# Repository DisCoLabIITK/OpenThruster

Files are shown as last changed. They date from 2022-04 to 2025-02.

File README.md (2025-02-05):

# OpenThruster
Open source 3D printed thruster for AUVs and ASVs.
---------------------------------------------------------------------------------------------------
3D Render:

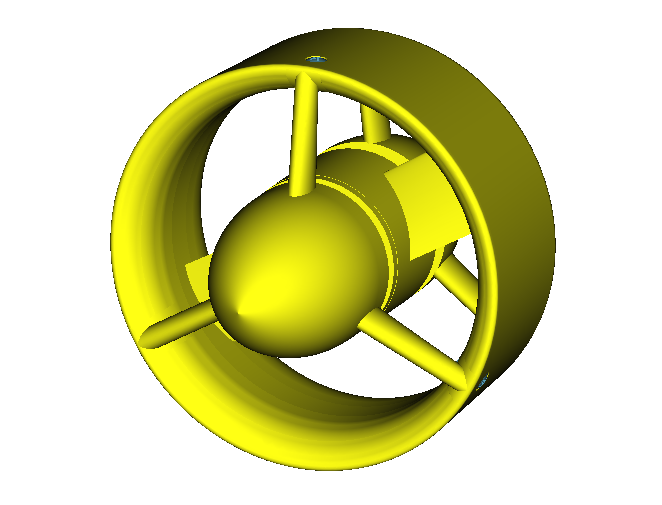
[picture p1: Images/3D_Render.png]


Exploded View:

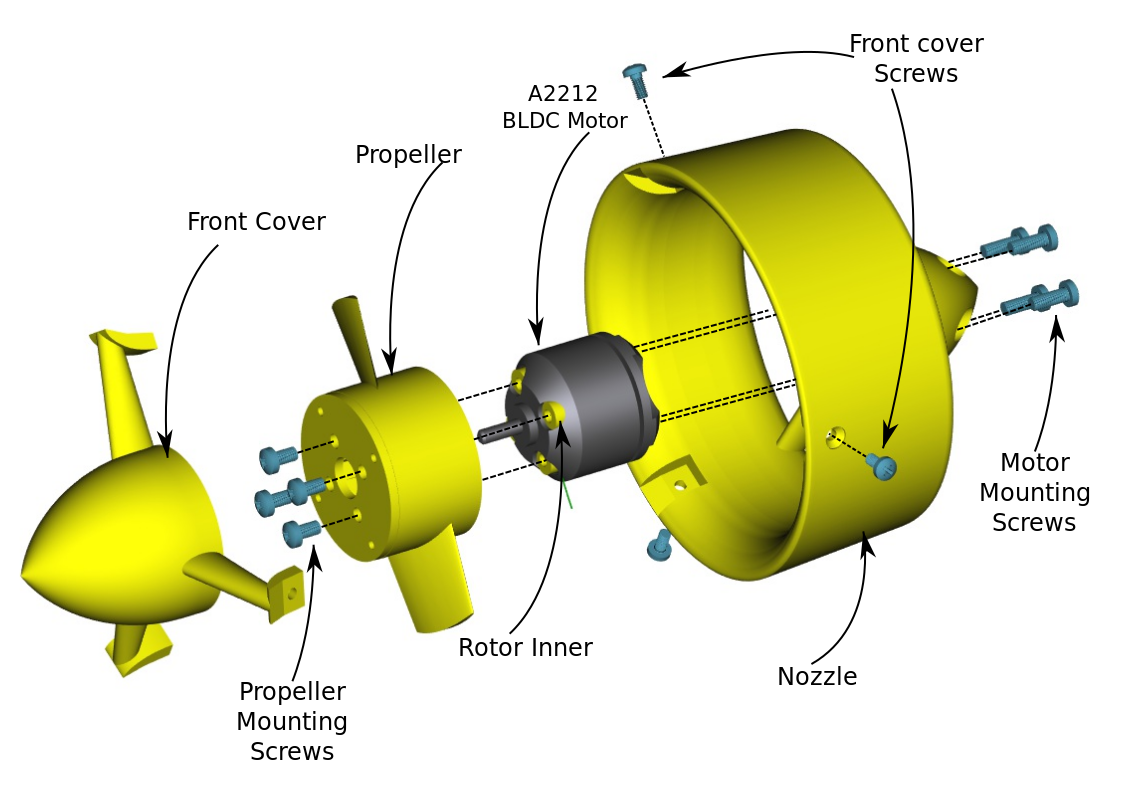
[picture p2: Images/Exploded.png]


Final Assembled:



Assembly
--------------------------------------------------------------------------------------------------
Assembly details on the Wiki page: [https://github.com/DisCoLabIITK/OpenThruster/wiki](https://github.com/DisCoLabIITK/OpenThruster/wiki/Assembly-Instructions)

The 3D printable STL files are in the STL folder.
--------------------------------------------------------------------------------------------------
Print settings for Nozzle:
* 0.4mm Extruder nozzle
* 0.2mm layer height
* 30% Infill (Gyroid)
* 4 Perimeters
* 6mm Brim.

Print settings for Propeller: 
* 0.1mm layer height
* 0.2-0.4mm Extruder nozzle
* Supports enabled
* 4 Perimeters
* Solid infill.

FreeCAD source files in FreeCAD source files folder. FreeCAD v0.19 was used for old design. New design files for FreeCad v1.0 are added in separate folder.

OpenProp source files downloaded from : https://openprop.engineering.dartmouth.edu/. The folder uploaded here has the modified option of NACA001612 and 001615 profiles.

Bill of Materials
--------------------------------------------------------------------------------------------------
1. PLA / ABS Filament for printing the propeller, nozzle, top cover and motor inner.
2. 3x M2.5 5mm Screws - Front Cover Screws
3. 4x M3 8mm Screws - Motor Mounting Screws
4. 1x A2212 1000KV BLDC Motor and the 4 screws (Propeller mounting screws in figure above) that come with it.
5. 1x 30A ESC with reversing capability

Testing Video: 
--------------------------------------------------------------------------------------------------
https://drive.google.com/file/d/1CwWSbAQDMGnaGXgHJ6uAxaj82aNr3GoJ/view?usp=sharing

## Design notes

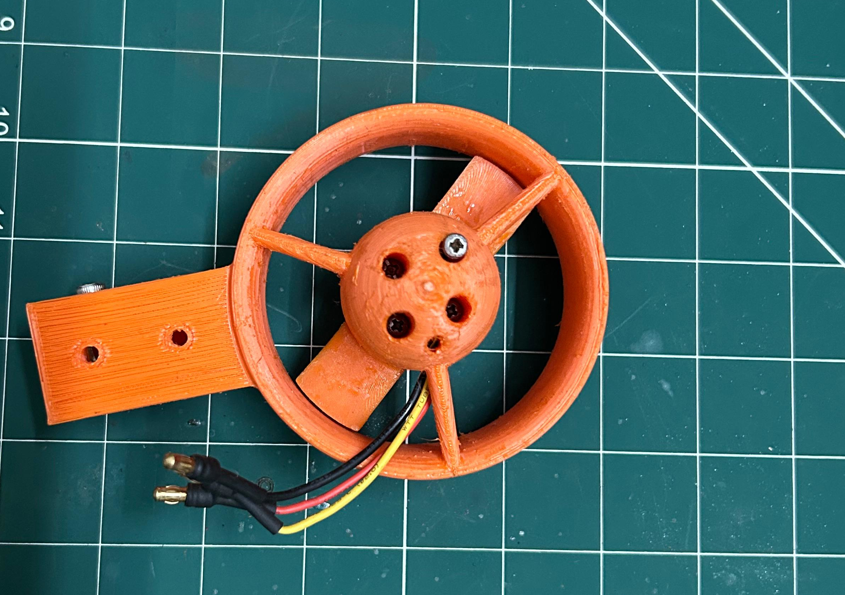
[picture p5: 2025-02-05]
Images/Motor_Nozzle_Screw.jpeg

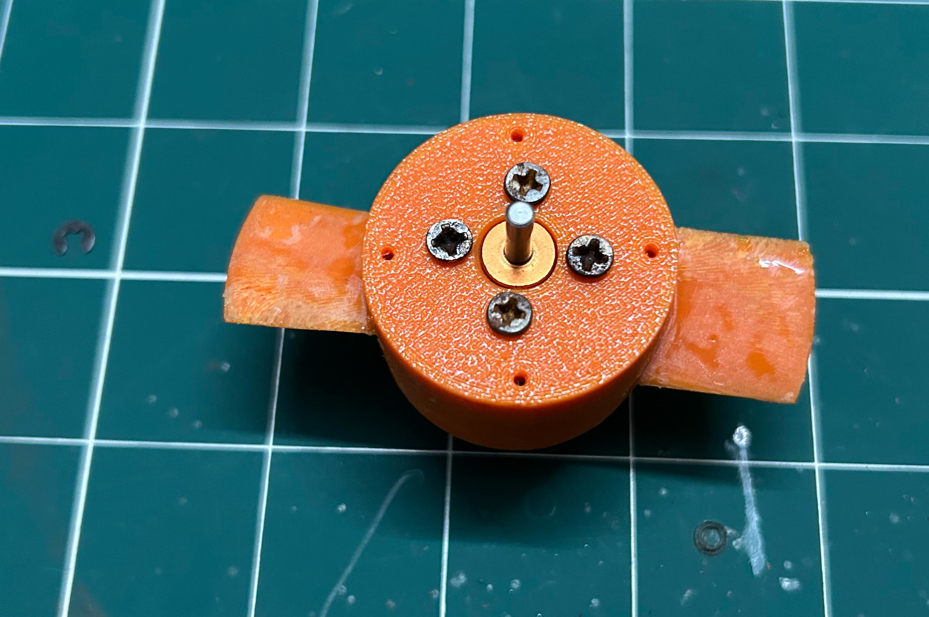
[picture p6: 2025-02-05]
Images/Propeller_Screw.jpeg

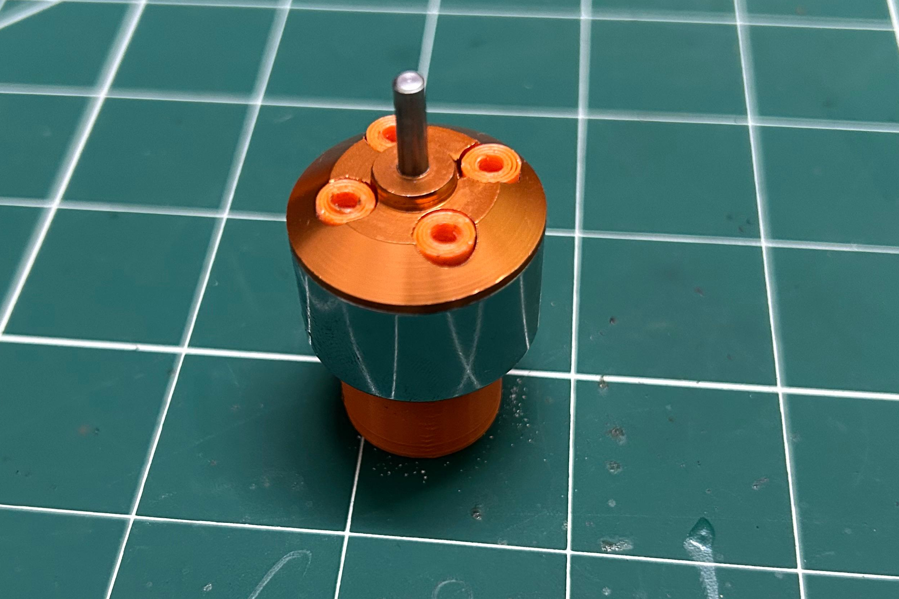
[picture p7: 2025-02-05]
Images/Use_Helper.jpeg

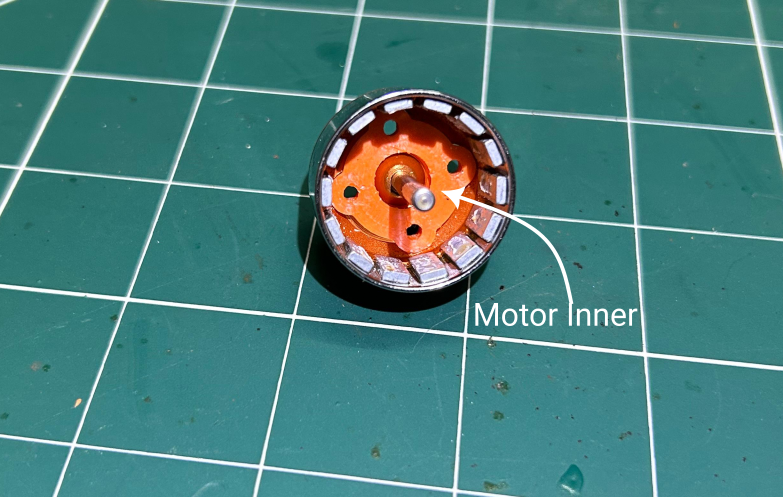
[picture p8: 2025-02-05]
Images/Insert_Inner.png

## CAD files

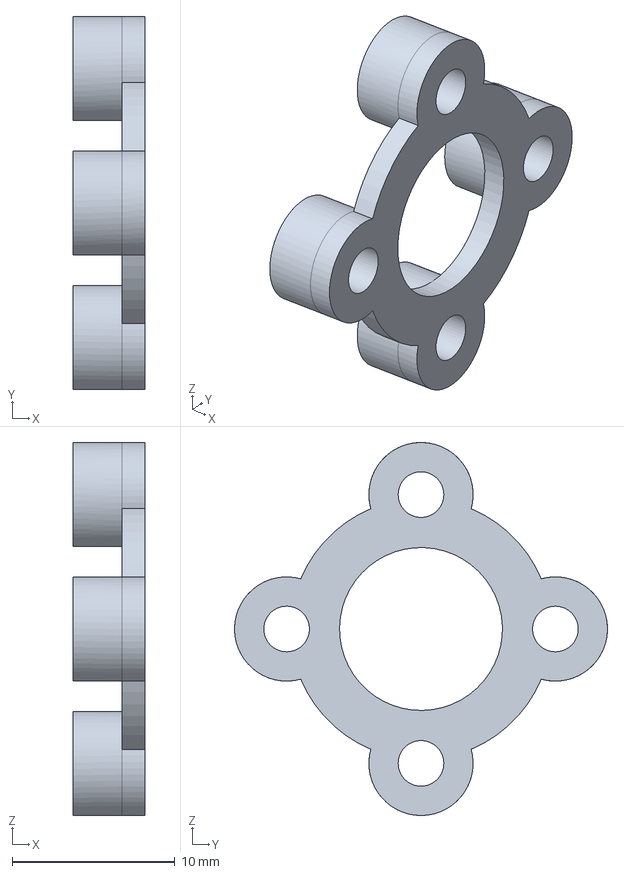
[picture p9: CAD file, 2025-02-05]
FreeCad_v_1.0_Source_Files/Motor_Inner_v2.FCStd
4.40 x 22.9 x 22.9 mm

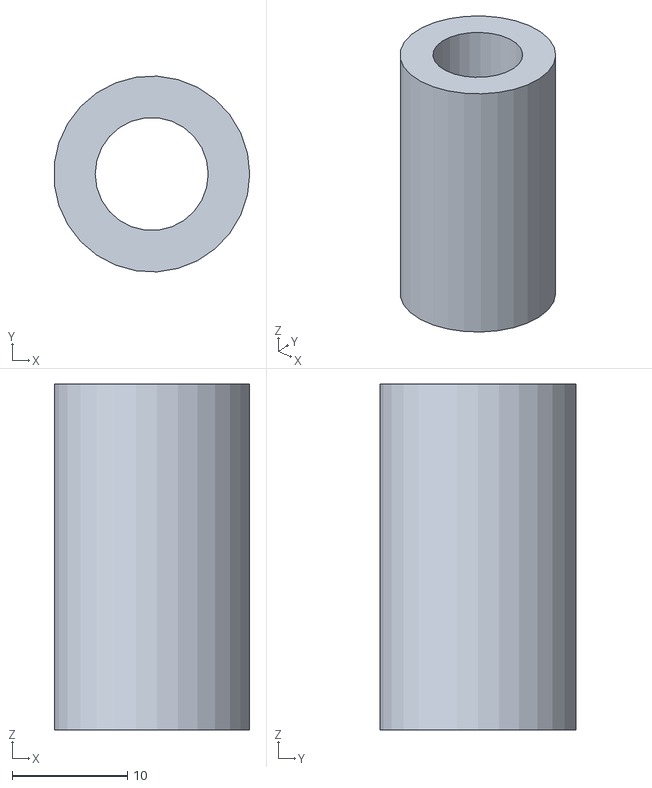
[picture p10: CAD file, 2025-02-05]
STL/Motor_Inner_Install_Helper.stl
17.0 x 17.0 x 30.0

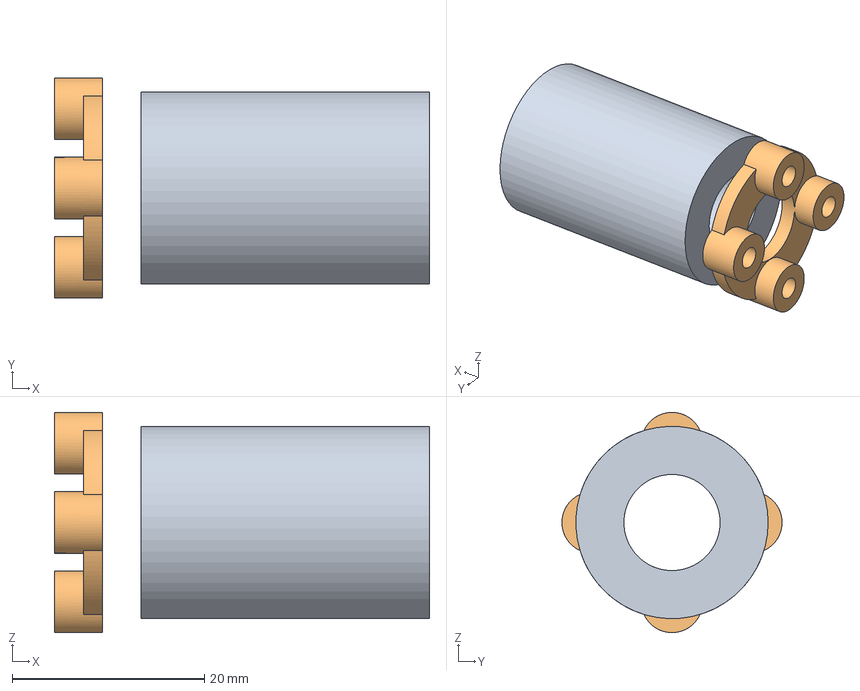
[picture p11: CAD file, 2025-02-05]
FreeCad_v_1.0_Source_Files/Motor_inner_Helper.FCStd
39.0 x 22.9 x 22.9 mm
Motor_Inner

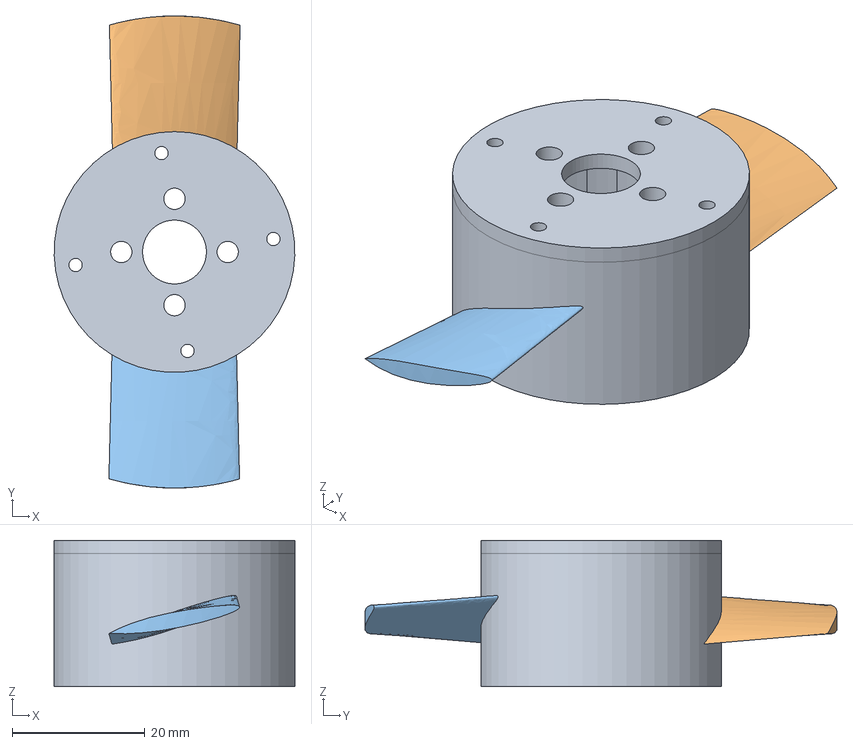
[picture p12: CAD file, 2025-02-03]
FreeCad_v_1.0_Source_Files/Prop-CCW.FCStd
36.2 x 71.0 x 22.0 mm
Hub
Blade1
Blade2

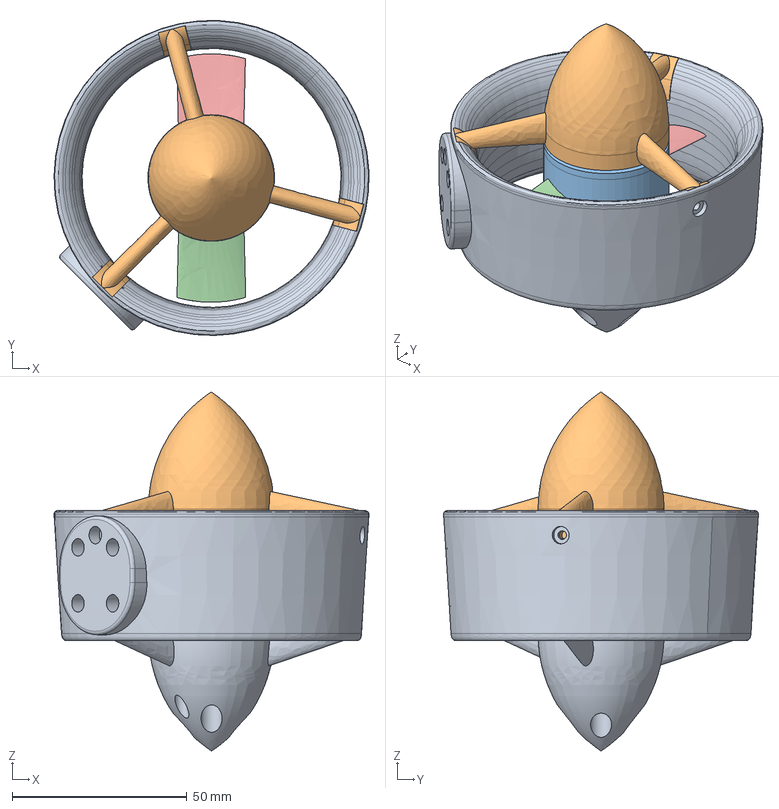
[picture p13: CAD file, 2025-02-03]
FreeCad_v_1.0_Source_Files/Thruster_ROV.FCStd
90.0 x 90.0 x 102.6 mm
Thruster_Nozzle001
Front_Cover
Hub
Blade2 (Mirror #1)
Blade1 (Mirror #2)

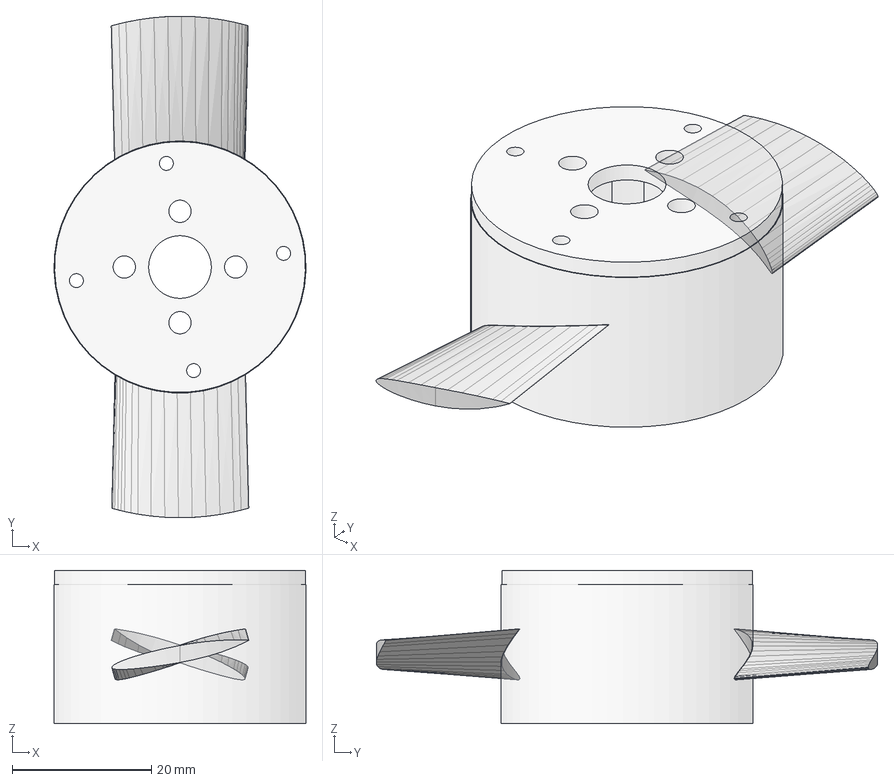
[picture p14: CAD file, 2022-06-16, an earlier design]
FreeCad_v_0.19_Source_Files/C4-28-5000-Thick-NonOpt-CW.FCStd
36.2 x 72.0 x 22.0 mm
NACA16-12
NACA16-013

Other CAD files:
STL/Motor_Inner.stl
STL/Prop-CW.stl
STL/Prop-CCW.stl
FreeCad_v_1.0_Source_Files/Prop-CW.FCStd
FreeCad_v_0.19_Source_Files/C4-28-5000-Thick-NonOpt-CCW.FCStd

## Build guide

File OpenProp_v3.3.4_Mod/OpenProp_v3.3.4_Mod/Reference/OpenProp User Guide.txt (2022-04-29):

OpenProp User Guide
10/21/2013

Prof. Brenden Epps,     Thayer School of Engineering at Dartmouth College
Prof. Richard Kimball,  Maine Maritime Academy

------------------------------------------------------------------------------------------------
Setup:

1. Download OpenProp_v3.3.3.zip from the OpenProp website: http://engineering.dartmouth.edu/openprop .  

2. Move the zip file to any convenient parent directory:
 	(e.g. <parent> == /Users/bepps/Documents/) 

3. Unzip OpenProp_v3.3.3.zip.  The "OpenProp" folder should now appear in the "parent" directory: 
	(e.g. <OpenProp> == /Users/bepps/Documents/OpenProp_v3.3.3/)

------------------------------------------------------------------------------------------------
Running OpenProp at the command line:

1. OpenProp can be run at the Matlab command line using various function calls.  The usage 
   is illustrated in the examples folders:

	./Examples/Ex*

2.  Use the templates in the Example folders to get started on your design.  The basic commands
    are as follows:
	>> Run_input_script, 			       (creates pt data structure and pt.input)
	>> pt.design   = EppsOptimizer(pt.input);
	>> pt.states   = Analyze(pt,[0:0.1:10]);
	>> pt.geometry = Geometry(pt);

3. Users are encouraged to create a new folder for each propeller/turbine design they create.  

------------------------------------------------------------------------------------------------
Running OpenProp using the graphical user interface (GUI):

1. OpenProp can also be run using the graphical user interface (GUI).

2. In Matlab, change the working directory to the "OpenProp" folder. 

3. At the command line, type:
	 >> openprop

	This loads the Single Design GUI.  

4. To perform a single propeller/turbine design, input the desired inputs to the GUI, and 
   press the "Run OpenProp" button.

   To perform a parametric design study, choose "Parametric Study" from the pull-down menu in
   the top left corner of the GUI.

------------------------------------------------------------------------------------------------
GUI file structure and data input/output:

1. In OpenProp, all propeller/turbine data is saved in a data structure called "pt".  

2. Upon execution of a "Single Design" or "Parametric Study", OpenProp will look for the
   directory <OpenProp>/filename/ and will create that directory if it does not exist:
  	(e.g. /Users/bepps/Documents/OpenProp_v3.3.2/DefaultPropeller)

   The pt data structure is always saved in <OpenProp>/filename/filename.mat .

   NOTE: When running a "Single Design", the following data structures are overwritten:
		pt.filename
		pt.date
		pt.input
		pt.design
		pt.geometry
		pt.states
	When running a "Parametric Study", the following data structures are overwritten:
		pt.name
		pt.date
		pt.parinput
		pt.paroutput

	In order to avoid overwriting previous designs, change the "filename".

3. In the "Single Design" and "Parametric Study" modes, the GUI values can be saved by 
   pressing the "Save" button.  This creates the following files:

	<OpenProp>/filename/filename_GUIsd.mat   -- "Single Design"    GUI values
	<OpenProp>/filename/filename_GUIps.mat   -- "Parametric Study" GUI values

   Similarly, prior GUI values can be loaded using the "Load" button and then choosing the
   appropriate GUI mat file. 

   NOTE: These files are automatically created/overwritten at runtime (i.e. when the 
         "Run OpenProp" button is pressed).

4. After running OpenProp, the "pt" data structure can be loaded into the Matlab workspace by:
    	>> change the working directory to <OpenProp>/filename
	>> load filename.mat

------------------------------------------------------------------------------------------------
Command line data input/output:

1. In OpenProp, all propeller/turbine data is saved in a data structure called "pt". 
   When running at the command line, the user may choose to use shorthand for the 
   "input", "design", "geometry", and "states" data structures, as follows:
	pt = 
		pt.filename
		pt.date
		pt.i
		pt.d
		pt.g
		pt.s

	For an example of this notation, see ExP02_Propeller_Parametric_Study.

2. The default inputs are listed in OpenProp_default_inputs.m, and the default input data 
   structure is as follows.  Here, "999" indicates that a value must be specified by the user.
   The user can create in input data structure that contains some or all of the other optional
   inputs.  See EppsOptimizer.m, Analyze.m, Geometry.m, and AnalyzeGeometry.m to understand the usage of these inputs.

	-----------------------------------
	input =
                part1: '------ Performance inputs ------'
                    L: 999  (only used in turbine   case)	% tip speed ratio     (for propeller, L  = pi/Js)
                   Js: 999  (only used in propeller case)	% advance coefficient (for turbine,   Js = pi/L )
                   CT: 999  (only used in propeller case)	% desired total thrust coefficient (propeller plus duct)         (user may specify 'KT' or dimensional 'THRUST' instead)
                   CQ: 999  (only used in propeller case)	% desired total torque coefficient (optional, in lieu of 'CT')   (user may specify 'KQ' or dimensional 'TORQUE' instead)
								% Note: The    user must specify one of {'CT', 'KT', or 'THRUST'} to minimize torque for prescribed thrust,
								%       or the user must specify one of {'CQ', 'KQ', or 'TORQUE'} to maximize thrust for prescribed  torque. 
								% Note: For turbine case, 'CT' and 'CQ' are unnecessary and are ignored
                part2: '------ Geometry inputs ------'
                    Z: 999 					% number of blades
             Meanline: 'NACA a=0.8 (modified)'			% meanline  form  (may be given as cell array of same length as XR)
            Thickness: 'NACA 65A010'				% thickness form  (may be given as cell array of same length as XR)
                part3: '------ Blade/Inflow inputs ------'
                   XR: [1x10 double]				% radial ordinate / R 
                 XCoD: [1x10 double]				% chord / D 			at XR
                Xt0oD: [1x10 double]				% thickness / D			at XR
                t0oc0: 0.1   * [1 1 1 1 1 1 1 1 1 1]		% thickness / chord		at XR (optional, in lieu of Xt0oD) 
                  XCD: 0.008 * [1 1 1 1 1 1 1 1 1 1]		% section drag coefficient	at XR
                  XVA: [1 1 1 1 1 1 1 1 1 1]			% axial inflow velocity / Vs	at XR
                  XVT: [0 0 0 0 0 0 0 0 0 0]			% swirl inflow velocity / Vs	at XR
                 dXVA: [0 0 0 0 0 0 0 0 0 0]			% variation in axial inflow velocity / Vs at XR (for cavitation analysis)
               XCLmax: [1x10 double]				% max lift coefficient	at XR       (for chord optimization)
                   ri: [1x10 double]				% [m] radial ordinate in dimensional units!         (optional)
                  VAI: [1 1 1 1 1 1 1 1 1 1]			% axial inflow velocity / Vs              at ri (optional, in lieu of  'XVA')
                  VTI: [0 0 0 0 0 0 0 0 0 0]			% swirl inflow velocity / Vs              at ri (optional, in lieu of  'XVT')
                 dVAI: [0 0 0 0 0 0 0 0 0 0]			% variation in axial inflow velocity / Vs at ri (optional, in lieu of 'dXVA')
                part4: '------ Computational inputs ------'
       Propeller_flag: 999					% 0 == turbine, 1 == propeller
         Viscous_flag: 999					% 0 == viscous forces off (CD = 0), 1 == viscous forces on
             Hub_flag: 0					% 0 == no hub, 1 == hub
            Duct_flag: 0					% 0 == no duct, 1 == duct
           Chord_flag: 0					% 0 == do not optimize chord lengths, 1 == optimize chord
            Plot_flag: 0					% 0 == do not display plots, 1 == display plots
            Wake_flag: 0					% 0 == Horseshoe(...,Wrench(...)) analytic formulae, 1 == Wake_Horseshoe(...) numerical model
 EppsOptimizer02_flag: 1   (only used in propeller case)	% Propeller optimization method (choose one only): LL-Linear
 EppsOptimizer23_flag: 0   (only used in propeller case)	% Propeller optimization method (choose one only): LL-Newton (standard    hub drag model)
 EppsOptimizer53_flag: 0   (only used in propeller case)	% Propeller optimization method (choose one only): LL-Newton (variational hub drag model)
      Make2Dplot_flag: 1					% 1 == make 2D geometry plot
      Make3Dplot_flag: 1					% 1 == make 3D geometry plot 
      Make_Rhino_flag: 0					% 1 == make Rhino file
      Make_SWrks_flag: 0					% 1 == make SolidWorks file
    QuarterChord_flag: 0					% 0 == lifting line at mid-chord, 1 == lifting line at mid-chord (for geometry only)
            LSGeoCorr: 'none'					% propeller Lifting Surface Geometry Corrections		
          ChordMethod: 'CLmax'					% Method of chord optimization {'CLmax', 'ConeyPLL', 'FAST2011dCTP', 'FAST2011dVAC'}
		  EAR: 0 					% Expanded Area Ratio specification (for chord optimization), ignored if EAR = 0
                   Mp: 20					% number of panels radially
                   Np: 20					% number of panels chordwise
                 ITER: 50					% number of iterations in solvers 
                  HUF: 0					% hub unloading factor
                  TUF: 0					% tip unloading factor
                  Rhv: 0.5					% hub vortex radius / hub radius
           ALPHAstall: 8*pi/180					% [rad] stall angle of attack
                part5: '------ Dimensional inputs (SI units) ------'
                   Vs: 1					% [m/s] free-stream speed
                    R: 1					% [m]	rotor radius (may give     diameter D    instead)
                 Rhub: 0.2000					% [m]   hub radius   (may give hub diameter Dhub instead)
                   Dm: 2					% [m]   model diameter 
                  rho: 1000					% [kg/m^3] fluid density
                    H: 3.0480					% [m]   shaft centerline depth (for cavitation analysis)
                    g: 9.8100					% [m/s^2] gravitational constant (for cavitation analysis)
                 Patm: 101325					% [Pa]  atmospheric pressure (for cavitation analysis)
                   Pv: 2500					% [Pa]  vapor pressure (for cavitation analysis)
                part6: '------ Duct inputs ------'
             Rduct_oR: 1					% duct radius  			 (user may specify dimensional 'Rduct' instead)
             Cduct_oR: 1					% duct chord length		 (user may specify dimensional 'Cduct' instead)
             Xduct_oR: 0					% duct axial position downstream (user may specify dimensional 'Xduct' instead)
                  CDd: 0.008					% duct drag coefficient
                  TAU: 1      (only used in propeller case)	% thrust ratio == propeller thrust / total thrust 
	          CTD: 0      (only used in turbine   case)     % desired duct thrust coefficient for turbine case (user may specify 'KTD' or dimensional 'THRUSTduct' instead)

	-----------------------------------
	design = 

        part1: '------ Section properties, size (1,Mp) ------'
           RC: [1x20 double] 					% radial coordinate of control points / R
           DR: [1x20 double] 					% delta(RV)
            G: [1x20 double] 					% circulation / (2*pi*R*Vs)
          VAC: [1x20 double] 					%      axial free-stream speed / Vs
          VTC: [1x20 double]					% tangential free-stream speed / Vs
       UASTAR: [1x20 double] 					%      axial inducted velocity / Vs
       UTSTAR: [1x20 double] 					% tangential inducted velocity / Vs
        VSTAR: [1x20 double] 					% total inflow speed / Vs
        TANBC: [1x20 double] 					% tangent of free-stream  inflow angle, Beta
       TANBIC: [1x20 double] 					% tangent of wake-aligned inflow angle, BetaI
           CL: [1x20 double] 					% section lift coefficient
           CD: [1x20 double] 					% section drag coefficient
          CoD: [1x20 double] 					% chord / diameter
         t0oc: [1x20 double] 					% thickness / chord
         t0oD: [1x20 double] 					% thickness / diameter
        part2: '------ Other properties  ------'
    converged: 1		 				% 1 == solver converged, 0 == solver did not converge
    iteration: 7	 					% iteration number at conclusion of solver
           RV: [1x21 double] 					% radial coordinate of vortex lattice points / R
      Rhub_oR: 0.2000 						% Rhub / R
          EAR: 0.6058 						% expanded area ratio
           LM: -0.3950 						% Lagrange multiplier
         VMIV: 1.0000 						% volumetric mean inflow velocity / Vs
         VMWV: 1.1825 						% volumetric mean wake   velocity / Vs
       SIGMAs: 257.4518 					% cavitation number
        part3: '------ Performance metrics ------'
            L: 3.7714 						% tip speed ratio
           Js: 0.8330 						% advance coefficient
           KT: 0.1500 						% thrust  coefficient
           KQ: 0.0283 						% torque  coefficient
           CT: 0.5505 						% thrust  coefficient
           CQ: 0.2076 						% torque  coefficient
           CP: 0.7831 						% power   coefficient
          CTH: -0.0077 						% hub thrust coefficient
         EFFY: 0.7030 						% efficiency
       ADEFFY: 0.8908 						% actuator disk efficiency
           QF: 0.7892 						% quality factor (EFFY/ADEFFY)

	-----------------------------------
 	states = 

        part1: '------ Off-design states ------'
            L: [18x1 double]					% tip speed ratio
           Js: [18x1 double]					% advance coefficient
           RC: [1x20 double]					% radial coordinate of control points / R
          CoD: [1x20 double]					% section chord length / rotor diameter
            G: [18x20 double]
       UASTAR: [18x20 double]					% ALL OTHERS SAME AS "design"
       UTSTAR: [18x20 double]
        VSTAR: [18x20 double]
        TANBC: [18x20 double]
       TANBIC: [18x20 double]
        ALPHA: [18x20 double] 					% net angle of attack
           CL: [18x20 double]
           CD: [18x20 double]
        part2: '------ Numerical metrics ------'
    converged: [18x1 double]
    iteration: [18x1 double]
        part3: '------ Performance metrics ------'
           KT: [18x1 double]
           KQ: [18x1 double]
           CT: [18x1 double]
           CQ: [18x1 double]
           CP: [18x1 double]
         EFFY: [18x1 double]
         VMWV: [18x1 double]

	-----------------------------------
	ginput =
                part1: '------ Design piont inputs ------'
                    L: 999  (only used in turbine   case)	% design point tip speed ratio     (for propeller, L  = pi/Js)
                   Js: 999  (only used in propeller case)	% design point advance coefficient (for turbine,   Js = pi/L )
								% Note: If the design point is unknown, use Js = pitch/diameter at blade tip

                part2: '------ Rotor geometry inputs ------'
                    Z: 999 					% number of blades
              Rhub_oR: 999   % the user must specify one of the following: {Rhub_oR or (Rhub and R) or (Dhub and D) or Dhub_oD}

                part3: '------ Blade/Inflow inputs ------'

Note: The blade geometry table must be given either versus raw radii 'XR' or control point radii 'RC'
                   XR  		RC				% radial ordinate / R   
           (computed)    	RV               		% vortex point radii / R
           (computed)    	DR               		% vortex panel width / R
                 XCoD  		CoD				% chord / D 			
  (XPoD or XTHETArad) 		(PoD or THETArad)		% pitch/diameter or pitch angle [rad]
                  XVA   	VAC				% axial inflow velocity / Vs
                  XVT  	 	VTC				% swirl inflow velocity / Vs                
                   Mp						% number of panels radially (default Mp = 20)
           
Note: IF CLCD_flag == 0, then the Meanline and Thickness distributions must be given to determine the lift and drag characteristics
                  XCD   	CD				% section drag coefficient	at XR
                f0oc0   	f0oc    			% section camber / chord at XR
      (Xt0oD or t0oc0)		t0oc				% thickness / D  or  thickness / chord  at XR 
            dCLdALPHA		dCLdALPHA  			% lift curve slope [default: dCLdALPHA = 2*pi/(1 + 2/PAR) ], where PAR = propeller aspect ratio (computed)
 
      For both the XR or RC data tables, the user must also provide either:
 
            {'f0octilde','CLItilde', and 'alphaItilde'} 	% {ideal camber, ideal lift coefficient, and ideal angle of attack} versus XR or RC
      or    {'Meanline' and 'Thickness'}			% meanline and thickness forms, which may be given as cell array of same length as XR or RC

      ELSE  CLCD_flag == 1, then the lift and drag coefficients must be given, tabulated versus radius and angle of attack:     
                            Note: angle of attack is measured relative to blade pitch angle THETArad, such that ALPHA == 0 when the inflow angle BetaIC equals THETArad   
         	      RELMdata      				% M == number of RELM  radii            (typically RELM == XR, but RELM can by any radii)        
        	     ALPHAdata  				% N == number of ALPHA angles of attack 
           		CLdata  				% CL(RELM,ALPHA) data matrix, size[M,N]
          		CDdata  				% CD(RELM,ALPHA) data matrix, size[M,N]      
      ENDIF

                part4: '------ Computational inputs ------'
       Propeller_flag: 999					% 0 == turbine, 1 == propeller
         Viscous_flag: 999					% 0 == viscous forces off (CD = 0), 1 == viscous forces on
             Hub_flag: 0					% 0 == no hub, 1 == hub
            Duct_flag: 0					% 0 == no duct, 1 == duct
            Plot_flag: 0					% 0 == do not display plots, 1 == display plots
            Wake_flag: 0					% 0 == Horseshoe(...,Wrench(...)) analytic formulae, 1 == Wake_Horseshoe(...) numerical model
            CLCD_flag: 0                                        % 0 == use CLCD_vs_ALPHA.m , 1 == use CL and CD data given in ginput
            LSGeoCorr: 'Morgan1968'  (propeller default)	% propeller Lifting Surface Geometry Corrections {'none', 'Morgan1968', 'EckhardtMorgan1955', 'vanManen1958'}		
            LSGeoCorr: 'none'        (turbine   default)	% propeller Lifting Surface Geometry Corrections - not recommended with turbines	
                 ITER: 50					% number of iterations in solvers 
                  Rhv: 0.5					% hub vortex radius / hub radius
           ALPHAstall: 8*pi/180					% [rad] stall angle of attack

------------------------------------------------------------------------------------------------	
Tips and tricks:

1. To save keystrokes, unpack the pt data structure.  For example, to plot the design
   circulation distribution:
   
	>> d = pt.design;
	>> figure,
	>> plot(d.RC,d.G)

    Or to plot a turbine performance curve:

	>> s = pt.states;
	>> figure,
	>> plot(s.L,-s.CP)

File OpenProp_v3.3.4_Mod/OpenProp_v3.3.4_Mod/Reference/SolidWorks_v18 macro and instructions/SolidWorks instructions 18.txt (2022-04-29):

SolidWorks instructions:
Created: Rob Damus,     9/24/2009
 Edited: Brenden Epps, 10/ 6/2009 

Follow these steps to create a solid propeller blade in SolidWorks:

___ Create your hub ----

1. Draw the hub in SolidWorks, and save it in a SolidWorks part document file

2. Copy your hub file and rename it something like hub_with_blades.swp

3. Open hub_with_blades.swp

4. Run the following steps to add the key blade to the hub:

--- Create the key blade ----

1. Export filename_SolidWorks.txt from the OpenProp Geometry function.
	-- Make sure that the trailing edge point (2Np-1) is the same as point (1), so all blade sections are closed contours.

2. Run the OpenProp SolidWorks macro:
	-- (In SolidWorks)  Tools > Macro > Edit
	-- Open SolidWorks_macro_v18.swp
	-- Press the play button
	-- This should result in a sketch of blade sections and guide curves over surface points.

3. Create Surface Loft of the SectionCurve1...SectionCurve21
	-- Select all 21 SectionCurves in the Feature Manager
	-- Insert > Surface > Loft  (orange loft button)
 	-- Select GuideCurves 1-6.  GuideCurve 7 is an artifact of Solidworks_macro_v14 and should be ignored in macro v18.
	-- Check "Merge tangent faces"
	-- Uncheck "Close loft"

3. Create Surface-Fill at tip
	-- Insert > Surface > Fill
	-- For Patch Boundary: select TipSectionCurve21
	-- For Constraint Curves: select all TipCurves
	-- Check "Fix up boundary" and "Optimize Surface"

4. Create Surface-Fill at root
	-- Insert > Surface > Fill
	-- For Patch Boundary: select RootSectionCurve1
	-- For Constraint Curves: select all RootCurves
	-- Check "Fix up boundary" and "Optimize Surface"

4. Knit surfaces into a solid
	-- Insert > Surface > Knit
	-- Select Surface-Loft, Boundary-Surface, Surface-Fill1, and Surface-Fill2
	-- Check "Try to form Solid"

If the stars align, you will generate a solid body for the blade, that will be accessible under the Solid Bodies node in the Feature Manager tree.

----- To create a propeller from the single blade -----

1. Draw the propeller axis
	-- Choose the line tool
	-- Select the Front Plane
	-- Select Horizontal orientation, "For construction", and "infinite length"
	-- Click on the origin to place the line along the X-axis
	-- Exit the sketch

2. Create Z blades
	-- Insert > Pattern/Mirror > Circular Pattern
	-- For the "Parameters": select the propeller axis, set the number of instances to Z, set the angle to 360 deg, and check "Equal spacing"
	-- For the "Bodies to Pattern": In the "Solid Bodies" folder in the Feature Manager tree, select "Surface-Knit1", which highlight the solid body of your propeller blade.
	-- 

3. Combine the blades and hub.
	-- In the Feature Manager tree, select the hub, key blade, and CirPattern (remaining blades).
	-- Insert > Features > Combine.
	-- Operation type is "Add"

4. Add a filet radius to the seam between blade and hub
	-- Insert > Features > Fillet/Round
	-- Fillet type = "Face fillet", Radius = 0.01 in, Items to fillet: select hub and blade
	-- Repeat this for each blade

1. Set the units to MKS or MMGS
	-- Tools > Options > Document Properties > Units
	-- Note: SolidWorks may not export dimensions correctly in MKS mode (i.e. The file says length is measured in meters, but dimensions are given in milimeters.)

___ Save STL file ----

1. File > Save as
	-- STL file format
	-- Note: click the "Options" button, and increase the resolution of the part for best 3D printing.

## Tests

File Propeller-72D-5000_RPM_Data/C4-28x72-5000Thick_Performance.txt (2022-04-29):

					 C4-28x72-5000Thick_Performance.txt 

					 OpenProp Performance Table

Date and time: 2022-04-20 12:07:44

 r/R	 V*	 beta	 betai	 Gamma	 CL	 Sigma	 dBetai
0.512	 9.58	 8.83	 19.48	 0.0400	 0.414	 2.740	 4.74
0.537	 10.17	 8.42	 18.24	 0.0398	 0.388	 2.433	 4.59
0.562	 10.61	 8.05	 17.50	 0.0398	 0.372	 2.234	 4.42
0.588	 11.07	 7.71	 16.87	 0.0399	 0.358	 2.053	 4.26
0.613	 11.54	 7.40	 16.29	 0.0400	 0.344	 1.890	 4.11
0.637	 12.00	 7.12	 15.75	 0.0401	 0.331	 1.746	 3.97
0.662	 12.47	 6.85	 15.25	 0.0402	 0.320	 1.617	 3.84
0.688	 12.94	 6.60	 14.77	 0.0403	 0.309	 1.501	 3.72
0.713	 13.41	 6.37	 14.33	 0.0403	 0.298	 1.398	 3.60
0.738	 13.88	 6.16	 13.92	 0.0404	 0.289	 1.304	 3.49
0.762	 14.36	 5.96	 13.54	 0.0404	 0.280	 1.220	 3.39
0.787	 14.83	 5.77	 13.18	 0.0404	 0.271	 1.144	 3.29
0.812	 15.30	 5.59	 12.85	 0.0405	 0.262	 1.075	 3.20
0.838	 15.77	 5.43	 12.55	 0.0405	 0.254	 1.012	 3.11
0.863	 16.23	 5.27	 12.26	 0.0404	 0.246	 0.954	 3.03
0.887	 16.70	 5.12	 11.99	 0.0404	 0.239	 0.901	 2.95
0.912	 17.17	 4.98	 11.73	 0.0403	 0.234	 0.853	 2.87
0.938	 17.64	 4.85	 11.47	 0.0403	 0.234	 0.808	 2.80
0.963	 18.10	 4.73	 11.20	 0.0401	 0.255	 0.767	 2.73
0.988	 18.61	 4.61	 10.80	 0.0399	 0.388	 0.725	 2.67

r/R 	 [ ], radial position of control points / propeller radius.
V* 	 [m/s], total inflow velocity.
beta 	 [deg], undisturbed flow angle.
betai 	 [deg], hydrodynamic Pitch angle.
Gamma 	 [m^2/s], vortex sheet strength.
CL 	 [ ], section lift coefficient.
Sigma 	 [ ], cavitation number.
d_alpha  [deg], inflow variation bucket width.

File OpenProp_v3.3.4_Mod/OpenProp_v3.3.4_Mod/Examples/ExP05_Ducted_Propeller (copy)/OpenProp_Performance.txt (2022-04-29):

					 OpenProp_Performance.txt 

					 OpenProp Performance Table

Date and time: 2022-01-20 17:45:15

 r/R	 V*	 beta	 betai	 Gamma	 CL	 Sigma	 dBetai
0.512	 23.19	 3.70	 7.73	 0.0138	 0.083	 0.477	 2.18
0.537	 24.32	 3.53	 7.34	 0.0137	 0.078	 0.433	 2.09
0.562	 25.45	 3.37	 7.05	 0.0137	 0.075	 0.396	 2.00
0.588	 26.58	 3.23	 6.77	 0.0137	 0.072	 0.363	 1.91
0.613	 27.71	 3.10	 6.52	 0.0136	 0.068	 0.334	 1.84
0.637	 28.84	 2.98	 6.28	 0.0136	 0.065	 0.308	 1.77
0.662	 29.97	 2.87	 6.06	 0.0135	 0.063	 0.285	 1.70
0.688	 31.10	 2.76	 5.85	 0.0134	 0.060	 0.265	 1.64
0.713	 32.23	 2.66	 5.66	 0.0134	 0.058	 0.247	 1.58
0.738	 33.37	 2.57	 5.49	 0.0133	 0.055	 0.230	 1.53
0.762	 34.50	 2.49	 5.33	 0.0132	 0.053	 0.215	 1.48
0.787	 35.63	 2.41	 5.17	 0.0131	 0.051	 0.202	 1.44
0.812	 36.76	 2.34	 5.03	 0.0129	 0.049	 0.190	 1.39
0.838	 37.89	 2.27	 4.90	 0.0128	 0.047	 0.178	 1.35
0.863	 39.02	 2.20	 4.77	 0.0127	 0.046	 0.168	 1.31
0.887	 40.15	 2.14	 4.65	 0.0126	 0.044	 0.159	 1.28
0.912	 41.28	 2.08	 4.55	 0.0125	 0.042	 0.150	 1.24
0.938	 42.41	 2.03	 4.44	 0.0124	 0.040	 0.142	 1.21
0.963	 43.54	 1.97	 4.35	 0.0123	 0.042	 0.135	 1.18
0.988	 44.67	 1.92	 4.24	 0.0123	 0.063	 0.128	 1.15

r/R 	 [ ], radial position of control points / propeller radius.
V* 	 [m/s], total inflow velocity.
beta 	 [deg], undisturbed flow angle.
betai 	 [deg], hydrodynamic Pitch angle.
Gamma 	 [m^2/s], vortex sheet strength.
CL 	 [ ], section lift coefficient.
Sigma 	 [ ], cavitation number.
d_alpha  [deg], inflow variation bucket width.

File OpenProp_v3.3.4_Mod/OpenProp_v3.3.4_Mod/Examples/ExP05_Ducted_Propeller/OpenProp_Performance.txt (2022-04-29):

					 OpenProp_Performance.txt 

					 OpenProp Performance Table

Date and time: 2022-01-17 15:55:01

 r/R	 V*	 beta	 betai	 Gamma	 CL	 Sigma	 dBetai
0.220	 6.92	 40.99	 48.46	 0.7155	 0.413	 5.223	 13.30
0.259	 7.64	 36.38	 43.99	 0.7819	 0.388	 4.262	 13.21
0.299	 8.41	 32.59	 40.17	 0.8637	 0.371	 3.501	 12.89
0.338	 9.22	 29.45	 36.85	 0.9445	 0.354	 2.901	 12.46
0.378	 10.05	 26.82	 33.97	 1.0193	 0.336	 2.428	 11.97
0.417	 10.91	 24.59	 31.45	 1.0861	 0.318	 2.054	 11.45
0.457	 11.77	 22.69	 29.26	 1.1448	 0.300	 1.754	 10.94
0.496	 12.65	 21.05	 27.32	 1.1955	 0.283	 1.511	 10.44
0.536	 13.54	 19.62	 25.61	 1.2384	 0.267	 1.313	 9.96
0.575	 14.44	 18.36	 24.09	 1.2739	 0.253	 1.149	 9.50
0.615	 15.34	 17.26	 22.73	 1.3017	 0.241	 1.013	 9.08
0.654	 16.25	 16.27	 21.51	 1.3216	 0.230	 0.899	 8.68
0.694	 17.16	 15.39	 20.40	 1.3323	 0.220	 0.802	 8.30
0.733	 18.08	 14.60	 19.40	 1.3322	 0.211	 0.719	 7.96
0.773	 19.00	 13.88	 18.49	 1.3179	 0.204	 0.648	 7.63
0.812	 19.92	 13.23	 17.66	 1.2848	 0.198	 0.586	 7.33
0.852	 20.84	 12.64	 16.89	 1.2252	 0.192	 0.533	 7.05
0.891	 21.77	 12.09	 16.19	 1.1267	 0.184	 0.486	 6.79
0.931	 22.69	 11.59	 15.54	 0.9663	 0.175	 0.445	 6.54
0.970	 23.62	 11.13	 14.93	 0.6896	 0.181	 0.408	 6.31

r/R 	 [ ], radial position of control points / propeller radius.
V* 	 [m/s], total inflow velocity.
beta 	 [deg], undisturbed flow angle.
betai 	 [deg], hydrodynamic Pitch angle.
Gamma 	 [m^2/s], vortex sheet strength.
CL 	 [ ], section lift coefficient.
Sigma 	 [ ], cavitation number.
d_alpha  [deg], inflow variation bucket width.

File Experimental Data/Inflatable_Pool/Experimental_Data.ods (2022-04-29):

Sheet: Data
Prop | 4000 |  |  |  | Prop | 4500
PWM | RPM | Thrust | Current | Power | PWM | RPM | Thrust | Current | Power
1050 | 4010 | 2160 | 18.6 | 210 | 1050 | 4700 | 2310 | 20 | 260
1100 | 3775 | 2130 | 17 | 190 | 1100 | 4400 | 2100 | 18.5 | 230
1150 | 3460 | 1760 | 14.8 | 163 | 1150 | 4010 | 1850 | 16.2 | 197
1200 | 3190 | 1441 | 12.3 | 140 | 1200 | 3600 | 1450 | 12.5 | 150
1250 | 2768 | 1150 | 9 | 100 | 1250 | 3130 | 1170 | 9 | 110
1300 | 2440 | 827 | 5.6 | 64 | 1300 | 2760 | 850 | 5.8 | 70
1350 | 1977 | 586 | 3 | 34 | 1350 | 2130 | 560 | 2.9 | 36
1400 | 1450 | 330 | 1.3 | 14 | 1400 | 1620 | 300 | 1.3 | 16.5
1450 | 820 | 92 | 0.4 | 5 | 1450 | 960 | 112 | 0.5 | 6.5
1500 | 0 | 0 | 0 | 0 | 1500 | 0 | 0 | 0 | 0
1550 | 1165 | 204 | 0.74 | 9 | 1550 | 1250 | 190 | 0.7 | 9.2
1600 | 1700 | 420 | 1.8 | 22 | 1600 | 1810 | 414 | 1.8 | 21.7
1650 | 2205 | 670 | 3.8 | 46 | 1650 | 2470 | 670 | 3.7 | 45.8
1700 | 2595 | 980 | 6.6 | 80 | 1700 | 2941 | 952 | 6.8 | 84.3
1750 | 3151 | 1300 | 10 | 120 | 1750 | 3360 | 1350 | 9.8 | 126
1800 | 3393 | 1560 | 12.6 | 145 | 1800 | 3920 | 1640 | 13.5 | 164
1850 | 3676 | 1850 | 15.5 | 176 | 1850 | 4010 | 2010 | 17 | 203
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

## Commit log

2022-06-16 Add files via upload
    Added the CW propeller.
    [C4-28-5000-Thick-NonOpt-CW.stl]
2022-09-12 Add files via upload
    Add correct 72mm dia. files.
    [Nozzle_72mm_v2-Front_Cover.stl, Nozzle_No_37_72mm_v2.stl]
2025-02-03 Adding new FC1.0 files and housekeeping
    [C4-28-5000-Thick-NonOpt-CCW.FCStd, C4-28-5000-Thick-NonOpt-CW.FCStd, Experimental_Data.ods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]
2025-02-05 Adding files for wiki.
    Adding image files for step by step assembly of the thruster.
2025-02-05 Removed unnecessary images and added new FC source files
    [Motor_Inner.stl, Motor_Inner_Install_Helper.stl, Motor_Inner_v2.FCStd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]
